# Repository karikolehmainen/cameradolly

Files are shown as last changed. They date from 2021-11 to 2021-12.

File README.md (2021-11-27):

# Camera Timelapse Dolly #
This camera dolly was born from desire to take moving timelapse videos in cold 
environment. Project has not evolved in features much since its conception 
during 2016 but in implementation much so. First implementation was using Adafruit
Motor HAT with NEMA17 stepper motors to move dolly and rotate camera head. Only new
feature is autamtec head alignment according to earth axis that has appeared 
since the first version. This is noe third revision. 
## Features ##
Summary of main high level features of the dolly
- Move camera along rail using timing belt
- End stops to detect end of rail
- Rotate camera 360° 
- Provide 8V power for camera (necessary in freezing conditions)
- Have lens heating element with temperature sensor
- Align camera rotation axis with earth axis for star tracking
- Control camera via USB interface
- Mobile app controls and 3G/4G connectivity

## Changes and rationale ##
Major change has been to ditch stepper motors in favour of DC motors. Main reason
behind the change was to enable star tracking and loooong exposures (like minutes
not seconds) as well as preserve energy. 
Also full size raspberry pi has been changes to Zero for more compact construction
and slightly less power consumption. Main drawback of this is the loss of 4G 
connectivity.

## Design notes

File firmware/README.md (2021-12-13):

# Instructions #

## Installation ##
TDB

## Interfaces ##

LMS303DHC Magnetometer / accelerometer in I2C bus 
- accelerometer address 0x24 
- magnetometer address 0x30

PCA9685 PWM interface for motoro contol in I2C bus
- address 0x60

ADS1115 ADC converter for battery measurement / temeperature sensor reading
- address 0x48

Head rotation sensor (gray code generator) on GPIO04 and GPIO18

Track rotation sensor (gray code generator) on GPIO13 and GPIO19

Endstop sensors (buttons) on GPIO20 and GPIO26

In ADC there are three channels of four in use
- Channel 0 input from current meter
- Channel 1 input from voltage divider for battery V
- Channel 3 input from lens temperature sensor 3.3/NTC

## MQTT Message Format ##
MQTT communication is migrating away from payload messages that were format <command>-<value>. Now commands are set with MQTT topics in format:
  /CameraDolly/<sub_topic> 
possible value is given in payload. For instace rotating camera head with specific angular speed can be given with following MQTT message:
  mosquitto_pub -h localhost -p 1883 -u cdolly -P dolly -t "CameraDolly/rotate" -m "0.004125296125"
Angular speed is given as degrees in second. Above command matches head rotation speed with earth angular speed

- "start": Start Dolly opration
- "stop": Stop Dolly operation

### /CameraDolly/rotate ###
Rotates camera head with anglural speed defined in the message body. Unit is degrees per second

### /CameraDolly/start ###
  Starts dolly operation. No parameters necessary
  
### /CameraDolly/stop ###
  Stops dolly opration. No parameters necessary
  
### /CameraDolly/gotostart ###
  Moves dolly to the begining of the track. No parameters necessary

### /CameraDolly/gotoend ###
  Moves dolly to the end of the track. No parameters necessary

### /CameraDolly/level_horizon ###
  Level Camera head with horizon. Seeks position so that accelerometer is level with horizon. No paramters necessary
  
### /CameraDolly/head_off ###
  Turns camera head off. This is reduntant with stop message but left here for possible case that only head would be turned off. No parameters necessary.

### /CameraDolly/measure_track ###
  Measure track by moving dolly from start to end and back. No parameters necessary.
  
### /CameraDolly/align_axis ###
  Align camera head with earth axis. As a paramter, give latitude of the camera in degrees e.g. 79.2344
  
### /CameraDolly/getcammodel ###
  Return cameramodel descriptor 
  
### /CameraDolly/getcamsettings ###
  Return JSON list of available camera settings.
  
### /CameraDolly/rcamsettings ###
  Return JSON list of current camera settings

### /CameraDolly/getheatsetting ###
  Returns lens heater setting
  
### /CameraDolly/setheat ###
  set lens heater to provided value. Value should be °C that the lens heater is set to
  
### Getters ###
- "cammodel": Retrieve Camera Model
- "camsettinglists": Return camera settings
- "getstepsize": Return dolly step size
- "getstepcount": Get number of steps so far
- "getmode": Return dolly operation mode
- "gettracking": Get tracking info
- "getimagenumber": return image numeber counter
- "getinterval": return image interval
- "getposition": transmit dolly position message
- "getheatsetting": return lens heater setting
### Setters ###
- "setheat (int)": set lens heater to °C temp 
- "setmode (int)": set dolly to operation mode enumeration
- "settargetx (double)": set tracing tarket X coordinate to x meters from rail start
- "settargety (double)": set tracing tarket Y coordinate to x meters perpenticular from rail
- "setstepdistance (int)": define distance on the rail between images in millimeters
- "setanglestep (float)": define angular distance of camerarotation between images
- "setdeclination (float)": define declination 
- "setcomperr (float)": set compass error
- "setimagenumber (int)": define how many images to take
- "interval (float)": define seconds between images
- "rotateccw": rotate head to counter clockwise direction
- "rotatecw": rotate head to clockwise direction
- "rcamsettings": trasmitt camera settings
- "get_head_angle": return camera head tilt angle

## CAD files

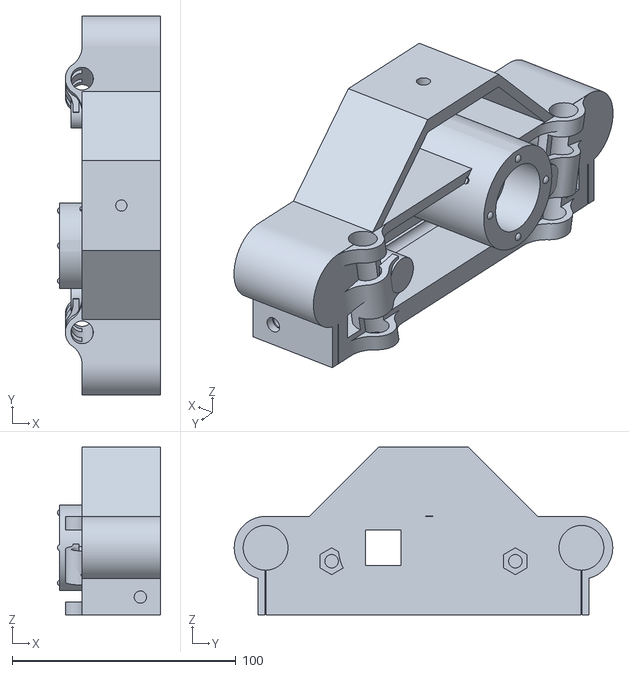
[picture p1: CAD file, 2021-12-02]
hardware/trackend_r.stl
46.0 x 169.0 x 75.0

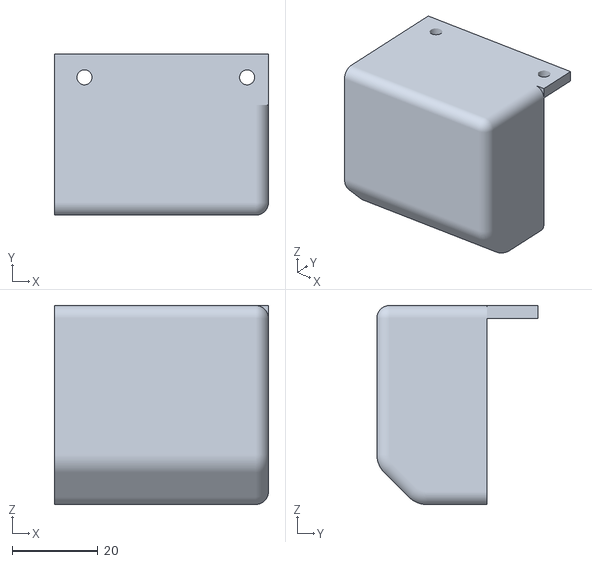
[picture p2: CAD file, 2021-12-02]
hardware/headmotor_cover.stl
50.0 x 37.7 x 46.5

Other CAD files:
hardware/trackend_l.stl

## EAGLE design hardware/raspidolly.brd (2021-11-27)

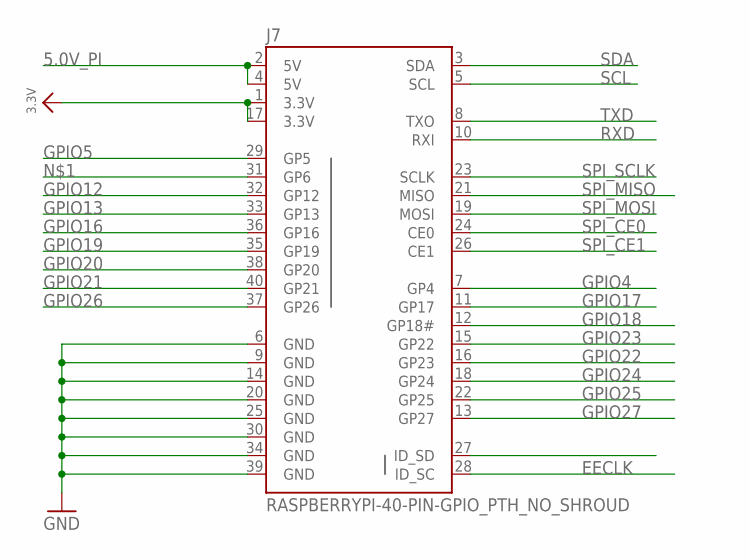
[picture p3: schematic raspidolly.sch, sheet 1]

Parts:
J7: RASPBERRYPI-40-PIN-GPIO_PTH_NO_SHROUD; 2X20

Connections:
3.3V: J7.1 (3.3V), J7.17 (3.3V); also elsewhere on the board
5.0V_PI: J7.2 (5V), J7.4 (5V); also elsewhere on the board
EECLK: J7.28 (ID_SC)
EEDATA: J7.27 (ID_SD)
GND: J7.6 (GND), J7.9 (GND), J7.14 (GND), J7.20 (GND), J7.25 (GND), J7.30 (GND), J7.34 (GND), J7.39 (GND); also elsewhere on the board
GPIO4: J7.7 (GP4); also elsewhere on the board
GPIO5: J7.29 (GP5)
GPIO12: J7.32 (GP12); also elsewhere on the board
GPIO13: J7.33 (GP13); also elsewhere on the board
GPIO16: J7.36 (GP16); also elsewhere on the board
GPIO17: J7.11 (GP17); also elsewhere on the board
GPIO18: J7.12 (GP18#); also elsewhere on the board
GPIO19: J7.35 (GP19); also elsewhere on the board
GPIO20: J7.38 (GP20); also elsewhere on the board
GPIO21: J7.40 (GP21); also elsewhere on the board
GPIO22: J7.15 (GP22)
GPIO23: J7.16 (GP23)
GPIO24: J7.18 (GP24)
GPIO25: J7.22 (GP25); also elsewhere on the board
GPIO26: J7.37 (GP26); also elsewhere on the board
GPIO27: J7.13 (GP27); also elsewhere on the board
RXD: J7.10 (RXI); also elsewhere on the board
SCL: J7.5 (SCL); also elsewhere on the board
SDA: J7.3 (SDA); also elsewhere on the board
SPI_CE0: J7.24 (CE0)
SPI_CE1: J7.26 (CE1)
SPI_MISO: J7.21 (MISO)
SPI_MOSI: J7.19 (MOSI)
SPI_SCLK: J7.23 (SCLK)
TXD: J7.8 (TXO); also elsewhere on the board

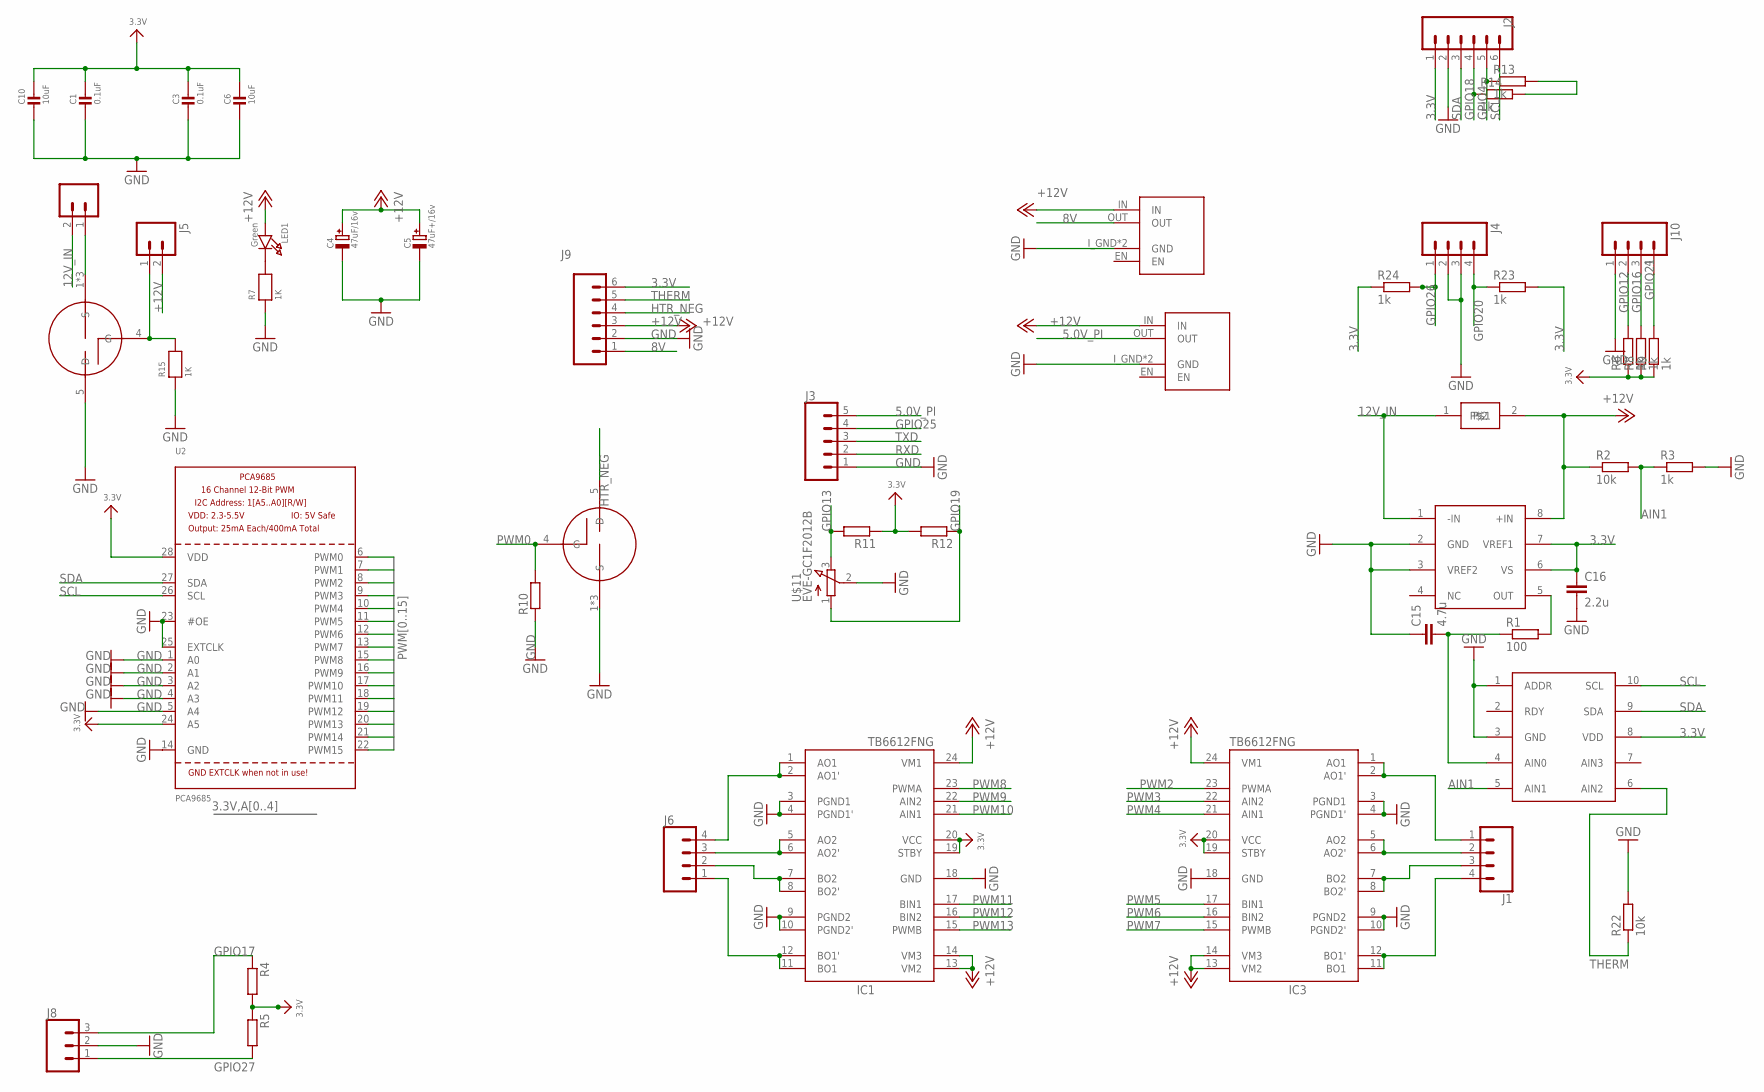
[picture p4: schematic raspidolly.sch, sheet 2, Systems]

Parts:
C1, C3: 0.1uF; 0805-NO
C4: 47uF/16v; PANASONIC_C
C5: 47uF+/16v; PANASONIC_C
C6, C10: 10uF; 0805-NO
C15: 4.7u; C0805
C16: 2.2u; C0805
IC1, IC3: TB6612FNG; SSOP24
J1, J6: CONN_04; 1X04
J2, J9: CONN_061.27MM; 1X06_1.27MM
J3: CONN_051.27MM; 1X05_1.27MM
J4, J10: M04JST; 1X04-1.5MM_JST
J5: M02PTH; 1X02
J8: CONN_03JST-PTH-VERT; JST-3-PTH-VERT
LED1: Green; CHIPLED_0805_NOOUTLINE
MPOWER: CONN_02; 1X02
R1: 100; R0805
R2, R22: 10k; R0805
R3, R6, R8, R9, R13, R14, R23, R24: 1k; R0805
R4, R5, R10, R11, R12: R-EU_R0805; R0805
R7, R15: 1K; 0805-NO
U2: PCA9685; TSSOP28
U$5, U$6: BUK9M; LFPAK33
U$8, U$10: UFH-BUCK
U$11: EVE-GC1F2012B; EVE
U$14: AD8418; MSOP08
U$15: ADS1015; VSSOP10
U$17: RESISTOR; 3921

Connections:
3.3V: C1.1, C3.1, C6.1, C10.1, C16.1, IC1.19 (STBY), IC1.20 (VCC), IC3.19 (STBY), IC3.20 (VCC), J2.1, J9.6, R4.2, R5.1, R6.1, R8.1, R9.1, R11.1, R12.2, R13.2, R14.2, R23.2, R24.1, U2.24 (A5), U2.28 (VDD), U$14.6 (VS), U$14.7 (VREF1), U$15.8 (VDD); also elsewhere on the board
5.0V_PI: J3.5, U$10.OUT; also elsewhere on the board
8V: J9.1, U$8.OUT
12V_IN: MPOWER.2, U$14.1 (-IN), U$17.1
+12V: C4.+, C5.+, IC1.13 (VM2), IC1.14 (VM3), IC1.24 (VM1), IC3.13 (VM2), IC3.14 (VM3), IC3.24 (VM1), J5.2, J9.3, LED1.A, R2.1, U$8.IN, U$10.IN, U$14.8 (+IN), U$17.2
AIN1: R2.2, R3.1, U$15.5 (AIN1)
GND: C1.2, C3.2, C4.-, C5.-, C6.2, C10.2, C15.1, C16.2, IC1.3 (PGND1), IC1.4 (PGND1'), IC1.9 (PGND2), IC1.10 (PGND2'), IC1.18 (GND), IC3.3 (PGND1), IC3.4 (PGND1'), IC3.9 (PGND2), IC3.10 (PGND2'), IC3.18 (GND), J2.2, J3.1, J4.2, J4.3, J8.2, J9.2, J10.1, R3.2, R7.1, R10.1, R15.1, R22.2, U2.1 (A0), U2.2 (A1), U2.3 (A2), U2.4 (A3), U2.5 (A4), U2.14 (GND), U2.23 (#OE), U2.25 (EXTCLK), U$5.1 (S), U$5.2 (S), U$5.3 (S), U$6.5 (D), U$8.I_GND (GND), U$8.O_GND (GND), U$10.I_GND (GND), U$10.O_GND (GND), U$11.2 (COM), U$14.2 (GND), U$14.3 (VREF2), U$15.1 (ADDR), U$15.3 (GND); also elsewhere on the board
GPIO4: J2.5, R13.1; also elsewhere on the board
GPIO12: J10.2, R6.2; also elsewhere on the board
GPIO13: R11.2, U$11.3 (B); also elsewhere on the board
GPIO16: J10.3, R8.2; also elsewhere on the board
GPIO17: J8.3, R4.1; also elsewhere on the board
GPIO18: J2.4, R14.1; also elsewhere on the board
GPIO19: R12.1, U$11.1 (A); also elsewhere on the board
GPIO20: J4.4, R23.1; also elsewhere on the board
GPIO21: J10.4, R9.2; also elsewhere on the board
GPIO25: J3.4; also elsewhere on the board
GPIO26: J4.1, R24.2; also elsewhere on the board
GPIO27: J8.1, R5.2; also elsewhere on the board
HTR_NEG: J9.4, U$5.5 (D)
unnamed: MPOWER.1, U$6.1 (S), U$6.2 (S), U$6.3 (S)
unnamed: IC1.1 (AO1), IC1.2 (AO1'), J6.4
unnamed: IC1.5 (AO2), IC1.6 (AO2'), J6.3
unnamed: IC1.7 (BO2), IC1.8 (BO2'), J6.2
unnamed: IC1.11 (BO1), IC1.12 (BO1'), J6.1
unnamed: J5.1, R15.2, U$6.4 (G)
unnamed: IC3.1 (AO1), IC3.2 (AO1'), J1.1
unnamed: IC3.5 (AO2), IC3.6 (AO2'), J1.2
unnamed: IC3.7 (BO2), IC3.8 (BO2'), J1.3
unnamed: R1.2, U$14.5 (OUT)
unnamed: IC3.11 (BO1), IC3.12 (BO1'), J1.4
unnamed: C15.2, R1.1, U$15.4 (AIN0)
unnamed: LED1.C, R7.2
PWM0: R10.2, U2.6 (PWM0), U$5.4 (G)
PWM1: U2.7 (PWM1)
PWM2: IC3.23 (PWMA), U2.8 (PWM2)
PWM3: IC3.22 (AIN2), U2.9 (PWM3)
PWM4: IC3.21 (AIN1), U2.10 (PWM4)
PWM5: IC3.17 (BIN1), U2.11 (PWM5)
PWM6: IC3.16 (BIN2), U2.12 (PWM6)
PWM7: IC3.15 (PWMB), U2.13 (PWM7)
PWM8: IC1.23 (PWMA), U2.15 (PWM8)
PWM9: IC1.22 (AIN2), U2.16 (PWM9)
PWM10: IC1.21 (AIN1), U2.17 (PWM10)
PWM11: IC1.17 (BIN1), U2.18 (PWM11)
PWM12: IC1.16 (BIN2), U2.19 (PWM12)
PWM13: IC1.15 (PWMB), U2.20 (PWM13)
PWM14: U2.21 (PWM14)
PWM15: U2.22 (PWM15)
RXD: J3.2; also elsewhere on the board
SCL: J2.6, U2.26 (SCL), U$15.10 (SCL); also elsewhere on the board
SDA: J2.3, U2.27 (SDA), U$15.9 (SDA); also elsewhere on the board
THERM: J9.5, R22.1, U$15.6 (AIN2)
TXD: J3.3; also elsewhere on the board

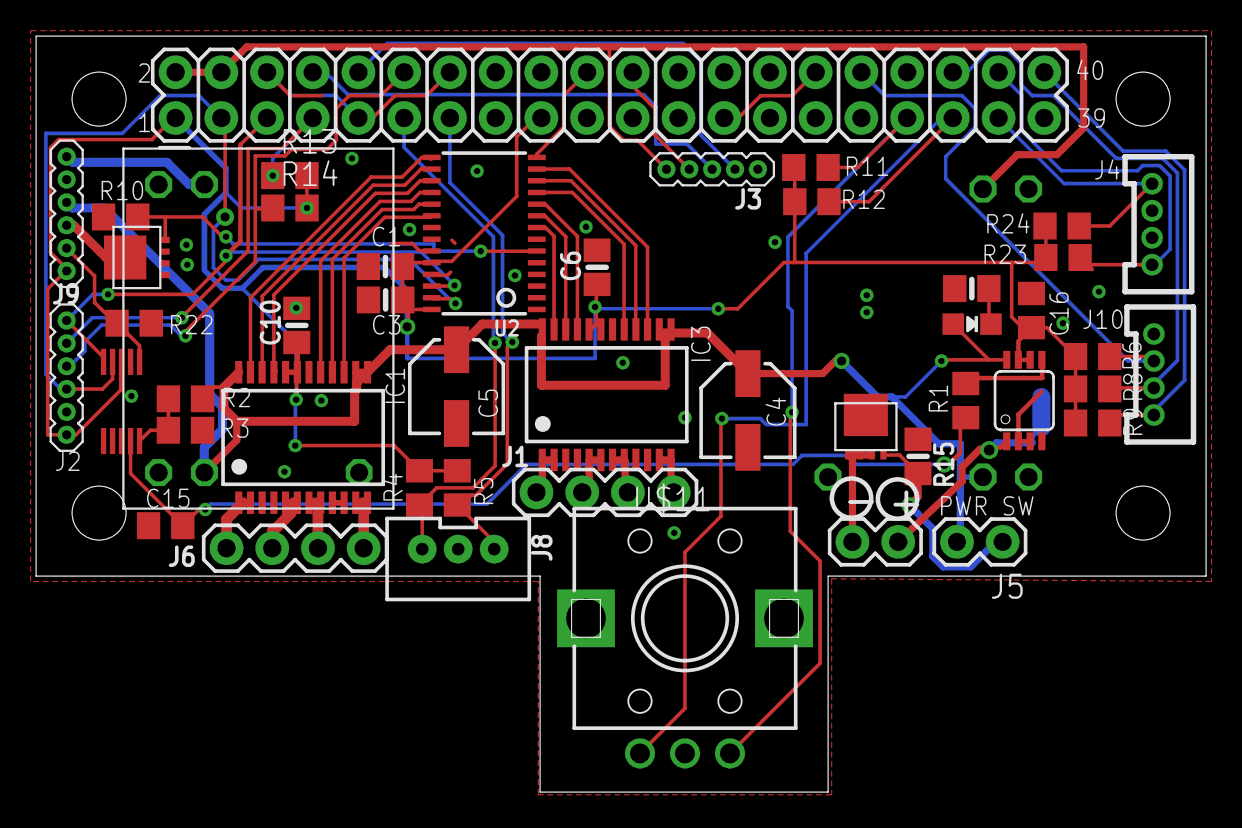
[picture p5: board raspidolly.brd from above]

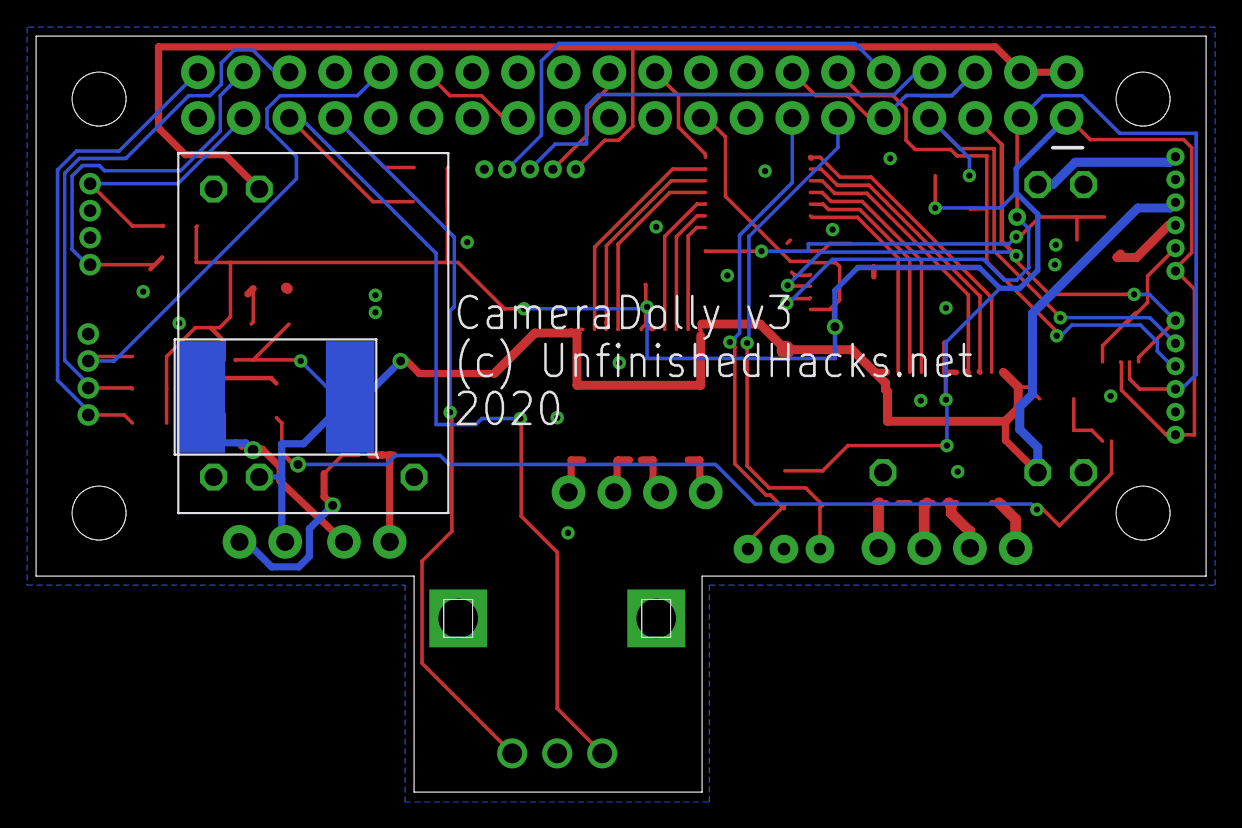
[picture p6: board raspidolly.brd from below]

Board: 2 copper layers, 65.0 x 42.0 mm, 49 parts (2 on the bottom side), 51 nets.

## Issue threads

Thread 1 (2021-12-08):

ADC values stuck

karikolehmainen, 2021-12-08:
possible ADC HW problem. Voltage divider on AN1 as well as current measurement on AN0 seem not to work

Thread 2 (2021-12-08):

Rotation encoder not working

karikolehmainen, 2021-12-08:
Possible hardware or wiring issue with rotary encoder detecting head rotation. Encoder fires interrupts on both GPIOs 04 and 18 but encoding steps does not work, hence the reading is unreliable. Could be an issue with slow rotation (3rpm motor) or wiring

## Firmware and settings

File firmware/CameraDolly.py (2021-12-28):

from __future__ import print_function
import os
import subprocess
import sys
import time
import atexit
import threading
import random
from Configuration import *
from Camera import *
from Dolly import *
from MessageBroker import *
from LensHeater import *

threads = []
stepcount = 0
numsteps = 0
counter = 0
I2CBUS = 1
# create empty threads (these will hold the stepper 1 and 2 threads)
st1 = threading.Thread()

mh = Adafruit_MotorHAT(addr=0x60,i2c_bus=I2CBUS,freq=3200)
#atexit.register(turnOffMotors)

def initiateThreads(datatrans,lensheater,configuration,dolly):
	t1 = threading.Thread(target=datatrans.worker)
	threads.append(t1)
	t1.start()

	t2 = threading.Thread(target=lensheater.worker)
	threads.append(t2)
	t2.start()

	t3 = threading.Thread(target=dolly.worker)
	threads.append(t3)
	t3.start()

	t4 = threading.Thread(target=dolly.getHead().worker)
	threads.append(t4)
	t4.start()

	print("started threads")

def getStepCount():
	return stepcount

def getCounter():
	return counter

def main():
	global stepcount
	global numsteps
	global counter
	conf = Configuration()
	conf.readConfiguration()

	images = conf.getDefaultImages()
			
	cam = Camera(conf)
	if (conf.isSimulation() == 0):
		cam.initCamera()

	dolly = Dolly(conf,mh)
	lensHeater = LensHeater(mh,conf)

	mBroker = MessageBroker(conf,cam,dolly,lensHeater)
	mBroker.connect()
	cam.setMessageBroker(mBroker)
	cam.setImageNumber(images)
	lensHeater.setMessageBroker(mBroker)
	initiateThreads(mBroker,lensHeater,conf,dolly)
	ts = time.time()
	stabbuffer = conf.getStabisationBuffer()
	print("main: going in the foreverloop (images="+str(images)+")")
	while (1):
		temperature = dolly.getTemp()
		voltage = dolly.getVoltage()
		current = dolly.getCurrent()
		power = int((voltage*current)/100000)/10.0
		#print("main: ADC values: temp: " + str(temperature) + ", power: " + str(power) + "W Voltage: "+str(int(voltage/100)/10.0)+"V")
		if (counter < cam.getImageNumber() and dolly.isRunning() == 1):
			print("main: Dolly running interval "+str((time.time()-(ts+dolly.getInterval()-stabbuffer))))
			counter = counter + 1
			# wait until enough time has passed since last photo. 
			ts = time.time()
			# Move dolly
			dolly.moveDolly()
			while (dolly.moving == True):
				time.sleep(0.1)
			print("\tDolly moved")
			while (time.time()<(ts+dolly.getInterval()-stabbuffer)):
				time.sleep(0.1)
			# Wait for awhile
			time.sleep(stabbuffer)
			# Capture image
			print("\tPicture take")
			cam.takePicture()
			print("\tPicture taken")
			mBroker.transmitPositionMessage(dolly.getPositionMM(), dolly.getAngleDeg(), counter, dolly.getHeading(), dolly.getTilt(),temperature,int(voltage/100)/10.0,power)
			lensHeater.setOn();
		else:
			lensHeater.setOff();
			counter = 0
			time.sleep(1)
		statusMsq = "{\"heading\":"+str(dolly.head.getHeadingDeg())+",\"running\":"+str(dolly.isRunning())+",\"head_status\":"+str(dolly.head.isRunning())+",\"position\":"+str(dolly.getPositionMM())+"}"
		mBroker.transmitdata(statusMsq, conf.getTopic()+"StatusMessage")
	dolly.quit()
	print("main: exiting the foreverloop")
	return 0

if __name__ == "__main__":
	sys.exit(main())

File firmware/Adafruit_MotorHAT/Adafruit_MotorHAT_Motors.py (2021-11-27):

import time

from Adafruit_MotorHAT.Adafruit_PWM_Servo_Driver import PWM


class Adafruit_StepperMotor:
    MICROSTEPS = 8
    MICROSTEP_CURVE = [0, 50, 98, 142, 180, 212, 236, 250, 255]

    #MICROSTEPS = 16
    # a sinusoidal curve NOT LINEAR!
    #MICROSTEP_CURVE = [0, 25, 50, 74, 98, 120, 141, 162, 180, 197, 212, 225, 236, 244, 250, 253, 255]

    def __init__(self, controller, num, steps=200):
        self.MC = controller
        self.revsteps = steps
        self.motornum = num
        self.sec_per_step = 0.1
        self.steppingcounter = 0
        self.currentstep = 0

        num -= 1

        if (num == 0):
            self.PWMA = 8
            self.AIN2 = 9
            self.AIN1 = 10
            self.PWMB = 13
            self.BIN2 = 12
            self.BIN1 = 11
        elif (num == 1):
            self.PWMA = 2
            self.AIN2 = 3
            self.AIN1 = 4
            self.PWMB = 7
            self.BIN2 = 6
            self.BIN1 = 5
        else:
            raise NameError('MotorHAT Stepper must be between 1 and 2 inclusive')

    def setSpeed(self, rpm):
        self.sec_per_step = 60.0 / (self.revsteps * rpm)
        self.steppingcounter = 0

    def oneStep(self, dir, style):
        pwm_a = pwm_b = 255

        # first determine what sort of stepping procedure we're up to
        if (style == Adafruit_MotorHAT.SINGLE):
            if ((self.currentstep//(self.MICROSTEPS//2)) % 2):
                # we're at an odd step, weird
                if (dir == Adafruit_MotorHAT.FORWARD):
                    self.currentstep += self.MICROSTEPS//2
                else:
                    self.currentstep -= self.MICROSTEPS//2
            else:
                # go to next even step
                if (dir == Adafruit_MotorHAT.FORWARD):
                    self.currentstep += self.MICROSTEPS
                else:
                    self.currentstep -= self.MICROSTEPS
        if (style == Adafruit_MotorHAT.DOUBLE):
            if not (self.currentstep//(self.MICROSTEPS//2) % 2):
                # we're at an even step, weird
                if (dir == Adafruit_MotorHAT.FORWARD):
                    self.currentstep += self.MICROSTEPS//2
                else:
                    self.currentstep -= self.MICROSTEPS//2
            else:
                # go to next odd step
                if (dir == Adafruit_MotorHAT.FORWARD):
                    self.currentstep += self.MICROSTEPS
                else:
                    self.currentstep -= self.MICROSTEPS

            pwm_a = pwm_b = 0
			
            if (self.currentstep >= 0) and (self.currentstep < self.MICROSTEPS):
                pwm_a = self.MICROSTEP_CURVE[self.MICROSTEPS - self.currentstep]
                pwm_b = self.MICROSTEP_CURVE[self.currentstep]
            elif (self.currentstep >= self.MICROSTEPS) and (self.currentstep < self.MICROSTEPS*2):
                pwm_a = self.MICROSTEP_CURVE[self.currentstep - self.MICROSTEPS]
                pwm_b = self.MICROSTEP_CURVE[self.MICROSTEPS*2 - self.currentstep]
            elif (self.currentstep >= self.MICROSTEPS*2) and (self.currentstep < self.MICROSTEPS*3):
                pwm_a = self.MICROSTEP_CURVE[self.MICROSTEPS*3 - self.currentstep]
                pwm_b = self.MICROSTEP_CURVE[self.currentstep - self.MICROSTEPS*2]
            elif (self.currentstep >= self.MICROSTEPS*3) and (self.currentstep < self.MICROSTEPS*4):
                pwm_a = self.MICROSTEP_CURVE[self.currentstep - self.MICROSTEPS*3]
                pwm_b = self.MICROSTEP_CURVE[self.MICROSTEPS*4 - self.currentstep]


        # go to next 'step' and wrap around
        self.currentstep += self.MICROSTEPS * 4
        self.currentstep %= self.MICROSTEPS * 4

        # only really used for microstepping, otherwise always on!
        self.MC._pwm.setPWM(self.PWMA, 0, pwm_a*16)
        self.MC._pwm.setPWM(self.PWMB, 0, pwm_b*16)

        # set up coil energizing!
        coils = [0, 0, 0, 0]

        step2coils = [[1, 0, 0, 0],[1, 1, 0, 0],[0, 1, 0, 0],[0, 1, 1, 0],[0, 0, 1, 0],[0, 0, 1, 1],[0, 0, 0, 1],[1, 0, 0, 1]]
        coils = step2coils[self.currentstep//(self.MICROSTEPS//2)]

        #print "coils state = " + str(coils)
        self.MC.setPin(self.AIN2, coils[0])
        self.MC.setPin(self.BIN1, coils[1])
        self.MC.setPin(self.AIN1, coils[2])
        self.MC.setPin(self.BIN2, coils[3])

        return self.currentstep

    def step(self, steps, direction, stepstyle):
        s_per_s = self.sec_per_step
        lateststep = 0
        print("{} sec per step".format(s_per_s))
        for s in range(steps):
            lateststep = self.oneStep(direction, stepstyle)
            time.sleep(s_per_s)

class Adafruit_DCMotor:
    def __init__(self, controller, num):
        self.MC = controller
        self.motornum = num
        pwm = in1 = in2 = 0

        if (num == 0):
                 pwm = 8
                 in2 = 9
                 in1 = 10
        elif (num == 1):
                 pwm = 13
                 in2 = 12
                 in1 = 11
        elif (num == 2):
                 pwm = 2
                 in2 = 3
                 in1 = 4
        elif (num == 3):
                 pwm = 7
                 in2 = 6
                 in1 = 5
        else:
            raise NameError('MotorHAT Motor must be between 1 and 4 inclusive')
        self.PWMpin = pwm
        self.IN1pin = in1
        self.IN2pin = in2

    def run(self, command):
        if not self.MC:
            return
        if (command == Adafruit_MotorHAT.FORWARD):
            self.MC.setPin(self.IN2pin, 0)
            self.MC.setPin(self.IN1pin, 1)
        if (command == Adafruit_MotorHAT.BACKWARD):
            self.MC.setPin(self.IN1pin, 0)
            self.MC.setPin(self.IN2pin, 1)
        if (command == Adafruit_MotorHAT.RELEASE):
            self.MC.setPin(self.IN1pin, 0)
            self.MC.setPin(self.IN2pin, 0)
    def setSpeed(self, speed):
        if (speed < 0):
            speed = 0
        if (speed > 255):
            speed = 255
        self.MC._pwm.setPWM(self.PWMpin, 0, speed*16)
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

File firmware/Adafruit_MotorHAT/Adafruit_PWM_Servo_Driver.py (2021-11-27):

# ============================================================================
# Adafruit PCA9685 16-Channel PWM Servo Driver
# ============================================================================
import logging
import math
import time


logger = logging.getLogger(__name__)


def get_i2c_device(address, i2c, i2c_bus):
    # Helper method to get a device at the specified address from the I2C bus.
    # If no i2c bus is specified (i2c param is None) then the default I2C bus
    # for the platform will be used.
    if i2c is not None:
        return i2c.get_i2c_device(address)
    else:
        import Adafruit_GPIO.I2C as I2C
        if i2c_bus is None:
            return I2C.get_i2c_device(address)
        else:
            return I2C.get_i2c_device(address, busnum=i2c_bus)


class PWM(object):
    # Registers/etc.
    __MODE1              = 0x00
    __MODE2              = 0x01
    __SUBADR1            = 0x02
    __SUBADR2            = 0x03
    __SUBADR3            = 0x04
    __PRESCALE           = 0xFE
    __LED0_ON_L          = 0x06
    __LED0_ON_H          = 0x07
    __LED0_OFF_L         = 0x08
    __LED0_OFF_H         = 0x09
    __ALL_LED_ON_L       = 0xFA
    __ALL_LED_ON_H       = 0xFB
    __ALL_LED_OFF_L      = 0xFC
    __ALL_LED_OFF_H      = 0xFD

    # Bits
    __RESTART            = 0x80
    __SLEEP              = 0x10
    __ALLCALL            = 0x01
    __INVRT              = 0x10
    __OUTDRV             = 0x04

    @classmethod
    def softwareReset(cls, i2c=None, i2c_bus=None):
        "Sends a software reset (SWRST) command to all the servo drivers on the bus"
        general_call_i2c = get_i2c_device(0x00, i2c, i2c_bus)
        general_call_i2c.writeRaw8(0x06)        # SWRST

    def __init__(self, address=0x66, debug=False, i2c=None, i2c_bus=None):
        self.regvals = [None] * 256
        self.i2c = get_i2c_device(address, i2c, i2c_bus)
        logger.debug("Reseting PCA9685 MODE1 (without SLEEP) and MODE2")
        self.setAllPWM(0, 0)
        self.i2c.write8(self.__MODE2, self.__OUTDRV)
        self.i2c.write8(self.__MODE1, self.__ALLCALL)
        time.sleep(0.005)                             # wait for oscillator
        mode1 = self.i2c.readU8(self.__MODE1)
        mode1 = mode1 & ~self.__SLEEP                 # wake up (reset sleep)
        self.i2c.write8(self.__MODE1, mode1)
        time.sleep(0.005)                             # wait for oscillator

    def setPWMFreq(self, freq):
        "Sets the PWM frequency"
        prescaleval = 25000000.0    # 25MHz
        prescaleval /= 4096.0       # 12-bit
        prescaleval /= float(freq)
        prescaleval -= 1.0
        logger.debug("Setting PWM frequency to %d Hz" % freq)
        logger.debug("Estimated pre-scale: %d" % prescaleval)
        prescale = math.floor(prescaleval + 0.5)
        logger.debug("Final pre-scale: %d" % prescale)
        oldmode = self.i2c.readU8(self.__MODE1);
        newmode = (oldmode & 0x7F) | 0x10             # sleep
        self.i2c.write8(self.__MODE1, newmode)        # go to sleep
        self.i2c.write8(self.__PRESCALE, int(math.floor(prescale)))
        self.i2c.write8(self.__MODE1, oldmode)
        time.sleep(0.005)
        self.i2c.write8(self.__MODE1, oldmode | 0x80)

    def setPWM(self, channel, on, off):
        "Sets a single PWM channel"
        self.i2c.write8(self.__LED0_ON_L+4*channel, on & 0xFF)
        self.i2c.write8(self.__LED0_ON_H+4*channel, on >> 8)
        self.i2c.write8(self.__LED0_OFF_L+4*channel, off & 0xFF)
        self.i2c.write8(self.__LED0_OFF_H+4*channel, off >> 8)

    def setAllPWM(self, on, off):
        "Sets a all PWM channels"
        self.i2c.write8(self.__ALL_LED_ON_L, on & 0xFF)
        self.i2c.write8(self.__ALL_LED_ON_H, on >> 8)
        self.i2c.write8(self.__ALL_LED_OFF_L, off & 0xFF)
        self.i2c.write8(self.__ALL_LED_OFF_H, off >> 8)

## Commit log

2021-11-27 added hw design files
    [raspidolly.brd, raspidolly.sch]
2021-11-29 ADC reading mods
2021-11-29 ADC dividers for volt&curr
2021-12-01 linear motor and end stops tested
2021-12-02 added STL files for track ends
    [headmotor_cover.stl, trackend_l.stl, trackend_r.stl]
2021-12-08 track measuring and head rotating works (possible HW problems with ADC)
    [CameraDolly.py, CameraHead.py, Dolly.py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]
2021-12-08 fixed bug in config file
    [Configuration.py, Dolly.py]
2021-12-08 some bug fixes & earth axis leveling now working
    [CameraDolly.py, CameraHead.py, MessageBroker.py]
2021-12-28 some updates to functions to get around HW bugs
    [CameraDolly.py, CameraHead.py, Dolly.py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]

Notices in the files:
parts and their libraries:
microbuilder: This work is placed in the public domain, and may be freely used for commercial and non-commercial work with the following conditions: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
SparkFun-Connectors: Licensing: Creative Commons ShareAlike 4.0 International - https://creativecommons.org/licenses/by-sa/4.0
